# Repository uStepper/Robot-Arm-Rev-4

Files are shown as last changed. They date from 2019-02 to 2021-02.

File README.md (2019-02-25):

# Robot Arm Rev 4
STL files and instructions for uStepper Robot Arm Rev 4

The Robot Arm and uStepper actuators can be purchased on www.ustepper.com/shop

<br /><span xmlns:dct="http://purl.org/dc/terms/" property="dct:title">uStepper</span> by <a xmlns:cc="http://creativecommons.org/ns#" href="www.ustepper.com" property="cc:attributionName" rel="cc:attributionURL">ON Development</a> is licensed under a <a rel="license" href="http://creativecommons.org/licenses/by-nc-sa/4.0/">Creative Commons Attribution-NonCommercial-ShareAlike 4.0 International License</a>.

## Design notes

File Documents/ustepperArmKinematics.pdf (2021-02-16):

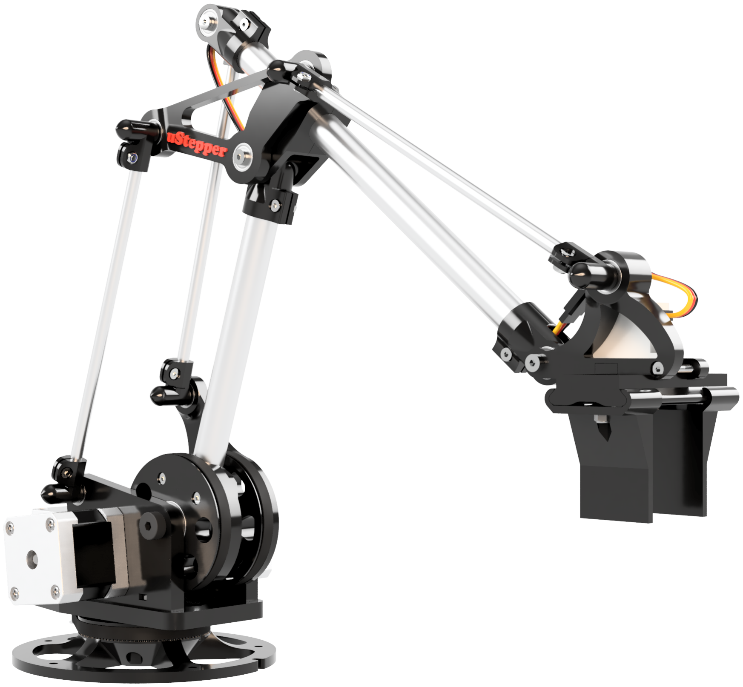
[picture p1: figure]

# uStepper Robot Kinematics

uStepper Robot Arm Rev 4 Kinematics

by Mogens Groth Nicolaisen

# Contents

1 uStepper Robot Arm Kinematics | 1

I

# uStepper Robot Arm Kinematics 1

To model the uStepper robot arm, first forward kinematic analysis is performed. The kinematic analysis is done analytical using basic trigonometry because of the Robot’s simple structure. D-H¹ with reference changing matrix transformations from world coordinates to end-effector could be done but is not required to derive kinematics for this simple setup.

## 1.1 Forward Kinematics

In the forward kinematics case, calculations are done to derive the end-effector point from a given set of actuator angles (θ). Figure 1.1 shows the basic geometry of the robot arm when looking from the side. Notice the offset from the end point to the "gripper" end point. This makes the model more generic when using different actuator types. An offset from this point to the actuator is required though. Another feature to notice is that when changing θ2
it is required to move both Primary and Secondary gear equally to maintain θ3
- this has to be accounted for in the implementation phase.

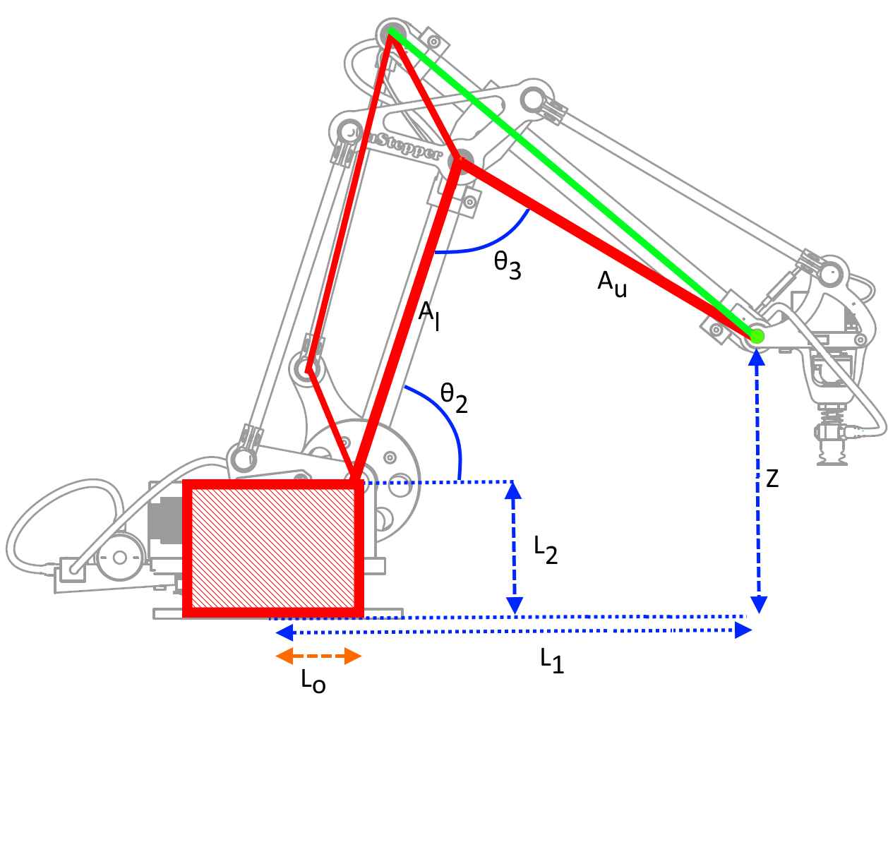
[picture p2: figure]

Figure 1.1: Side view of the robot, with simple graphics applied to help deriving the kinematic equations.

From Figure 1.5 it is easily seen that to account for the offset from end-point to actuator end-point an offset in Z and L1

is required. These are denoted Zo and L1o respectively and for the actuator on Figure 1.5 Zo would be negative while L1o would be positive. The offsets are omitted in the following derivations to ease the readability. In the code they are added.

1Denavit–Hartenberg
1

2 | Chapter 1. uStepper Robot Arm Kinematics

Using the geometry presented in Figure 1.1 Z is derived by adding right triangles resulting in the more detailed Figure 1.2

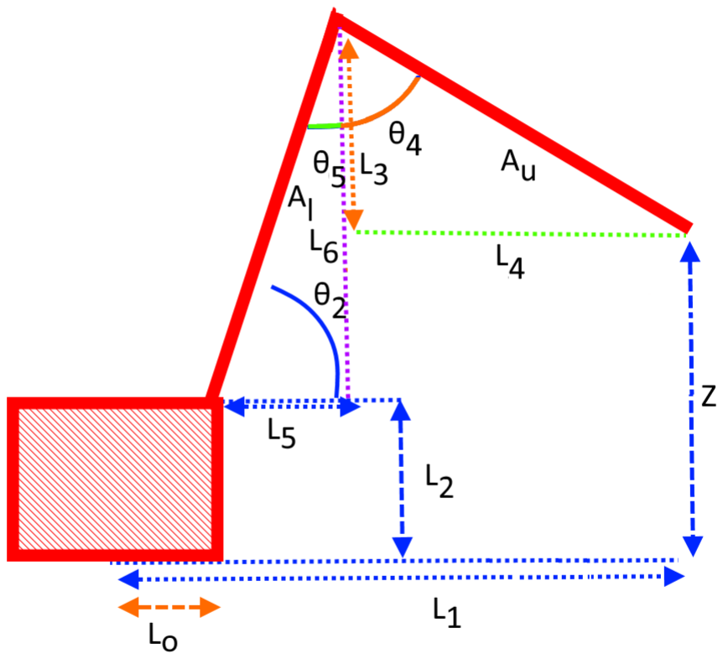
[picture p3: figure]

Figure 1.2: Side view of the robot arm representation for kinematics calculations.

Using Figure 1.2 Z will be derived as shown Equation (1.1):

Z = L2 + L6 − L3
[mm] (1.1)

Where L3 and L6 will be derived using simple trigonometry and L2 is a design parameter from Table 1.1. First L6

is derived in Equation (1.3)

sin(θ2

) = L6
Al

(1.2)

L6 = sin(θ2
)Al

[mm] (1.3)

To derive L3

it is required to know θ4

, which is possible to derive from θ5 found in Equation (1.4):

θ5 = 180◦ − (90◦ + θ2

) | [◦
] (1.4)

Where the 180◦

comes from the angle sum of a triangle, and the 90◦ | from the known right angle. The
angle θ2 was given as input to the forward kinematics as discussed previously. θ4
is derived in Equation (1.5):

θ4 = θ3 − θ5

| [ ◦
] (1.5)

And L3

is found from Equation (1.7)

cos(θ4

) = L3
Au

(1.6)

L3 = cos(θ4
)Au
| [mm] (1.7)

1.1. Forward Kinematics | 3

Z can now be derived using Equation (1.1) stated here again for convenience:

Z = L2 + L6 − L3 | [mm] (1.8)

Now that Z is derived, X and Y is left. To derive those the view is changed to the top view in Figure 1.3.

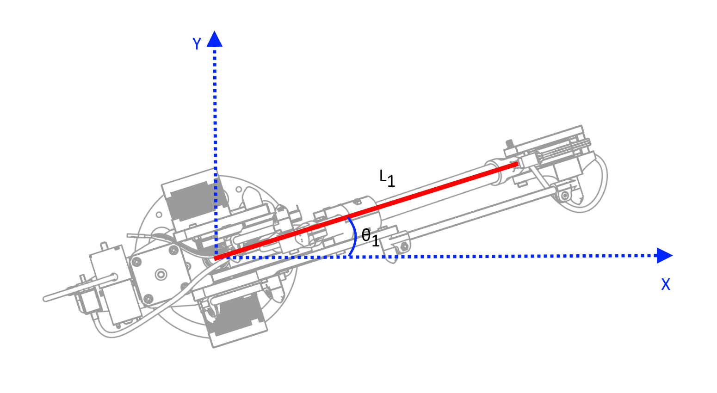
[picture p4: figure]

Figure 1.3: Top view of the robot arm with world coordinates on top.

As also shown on Figure 1.1, Figure 1.3 shows the stretch L1

. Additionally the rotation angle θ1 is marked
on Figure 1.3. Using simple trigonometry X and Y is derived in Equation (1.12).

cos(θ1

) = X
L1

(1.9)

X = cos(θ1
)L1

[mm] (1.10)

sin(θ1

) = Y
L1

(1.11)

Y = sin(θ1
)L1

[mm] (1.12)

Looking at Figure 1.2 it is obvious that L1 is the sum of L4 and L5

. L5

is derived using regular trigonometry in Equation (1.14).

cos(θ2

) = L5
Al

(1.13)

L5 = cos(θ2
)Al

[mm] (1.14)

And finally L4

is found from Equation (1.16).

sin(θ4

) = L4
Au

(1.15)

L4 = sin(θ4
)Au

[mm] (1.16)

Arriving at L1

in Equation (1.17).

L1 = L4 + L5 + Lo

[mm] (1.17)

4 | Chapter 1. uStepper Robot Arm Kinematics

Where Lo

is the constant offset from rotation center. To sum up, Z, X and Y is found by the following combined equations (from the previous derivations):

Z = L2 + L6 − L3 | [mm] (1.18)

Z = L2 + sin(θ2

)Al − cos(θ3 − (90◦ − θ2
))Au
| [mm] (1.19)

X = cos(θ1
)L1
| [mm] (1.20)

X = cos(θ1

)(sin(θ3 − (90◦ − θ2

## ))Au + cos(θ2 )Al + Lo

) | [mm] (1.21)

Y = sin(θ1
)L1
| [mm] (1.22)

Y = sin(θ1

)(sin(θ3 − (90◦ − θ2

## ))Au + cos(θ2 )Al + Lo

) | [mm] (1.23)

### 1.1.1 Summing Up

To implement the forward kinematics the former derived equations can be arranged to reduce computations required. This will be done in the following, and a code example will be presented.
The former enabled us to calculate the coordinates based on our angles θ1
| , θ2 and θ3 . But we intend to
read out motor angles, so we have to do a little conversions when reading motor angles:

θ1 = θM B

1
K

[

| ◦ ] (1.24)

θ2 = (θM E − θMS)

1
K

[

◦
] (1.25)

θ3 = θMS

1
K

[

◦
] (1.26)

where θM B is base motor angle, θM E is elbow motor angle, θMS is shoulder motor angle and K is the gear ratio which is the same for all three gears in this case. The inputs for the forward kinematics are then as derived from the motor angles:

- θ1
- rotation angle
- θ2
- shoulder angle
- θ3
- elbow angle

And the required equations are:

Z = L2 + sin(θ2

)Al − cos(θ3 − (90◦ − θ2
))Au

[mm] (1.27)

k1 = (sin(θ3 − (90◦ − θ2

## ))Au + cos(θ2 )Al + Lo

) | [ ] (1.28)

X = cos(θ1
)k1

[mm] (1.29)

Y = sin(θ1
)k1

[mm] (1.30)

A code example snippet is provided in the following (note that Zo and L1o are added here as discussed in Section 1.1):

1.2. Inverse Kinematics | 5
1 | // Pre−c a l c u l a t e d o f f s e t s i n motor an gle a t home p o s i t i o n
2 | #d e fi n e SHOULDEROFFSET 142.0 f
3 | #d e fi n e ELBOWOFFSET 45.0 f

4
5 | void u S te p pe rR o b o ti c s : : FWKinematic ( f l o a t& x , f l o a t& y , f l o a t& z , f l o a t thetaMB , f l o a t thetaME
| , f l o a t thetaMS ) //Forward ki nem a ti c s an gle To xyz
6 | {

7
8 | t he t a 1 = thetaMB∗1/K ;
9 | t he t a 2 = ( thetaME−thetaMS ) ∗1/K + ELBOWOFFSET ;
10 | t he t a 3 = thetaMS∗1/K + SHOULDEROFFSET ;

11
12 | t he t a 1 = t he t a 1 ∗ 3.1415 / 18 0.0 ; // To r a di a n s
13 | t he t a 2 = t he t a 2 ∗ 3.1415 / 18 0.0 ; // To r a di a n s
14 | t he t a 3 = t he t a 3 ∗ 3.1415 / 18 0.0 ; // To r a di a n s

15
16 | z = L2 + si n ( t he t a 2 ) ∗Al − co s ( t he t a 3 − (90 − t he t a 2 ) ) ∗Au + Zo ; // o f f s e t i n the Z di r e c t o n
| f o r the a c t u a t o r i s added here

17
18 | k1 = si n ( t he t a 3 − (90 − t he t a 2 ) ) ∗Au + co s ( t he t a 2 ) Al + Lo + L1o ; // o f f s e t i n the L1 di r e c t o n
| f o r the a c t u a t o r i s added here

19
20 x = co s ( t he t a 1 ) ∗k1 ;

21
22 y = si n ( t he t a 1 ) ∗k1 ;

23
24 }

Another thing to notice here is the offset added to ELBOW and SHOULDER - these offsets are defined by the home-position of the robot which is at the mechanical stops where the arm is retracted to towards the base

## 1.2 Inverse Kinematics

To control the robot end-effector reference positions are given in the world coordinate system, which then has to be translated to a given set of actuator angles achieving these reference positions. I.e. in the inverse kinematics case, the desired end-effector coordinates are known and from these the actuator angles must be derived.
The starting point of the inverse kinematics derivation is the rotation angle. Looking at Figure 1.4 it is obvious that simple trigonometry where a right angle triangle is constructed from the end of L1 down to the x-axis, can be used.

6 | Chapter 1. uStepper Robot Arm Kinematics

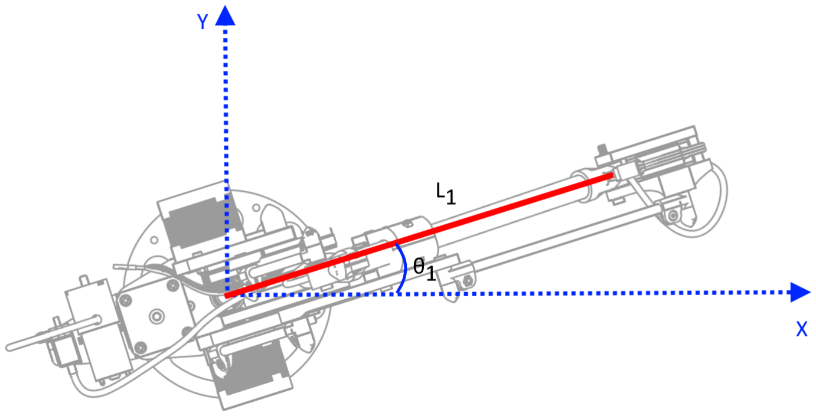
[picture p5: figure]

Figure 1.4: Top view of the robot arm with world coordinates on top.

To derive θ1 Equation (1.31) is used.

θ1 = a tan2 (Y, X) | [ ◦ ] (1.31)

Using a tan2 provides solutions for X = 0 and X < 0 as opposed to the regular arctangent function where solutions for these cases has to be handled separately.
For the next calculations the length of L1 | is required and therefore found in Equation (1.32).

L1 =

p
X² + Y ² | [mm] (1.32)

To derive the remaining two angles a new figure is constructed (Figure 1.5).

1.2. Inverse Kinematics | 7

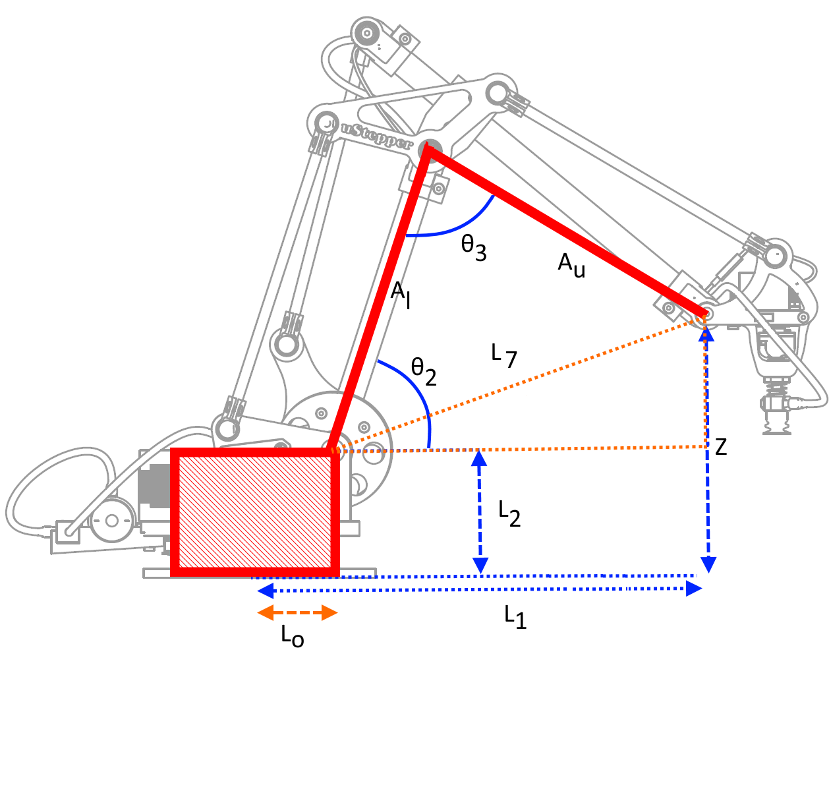
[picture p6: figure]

Figure 1.5: Side view of the robot, with simple graphics applied to help deriving the kinematic equations.

First θ3
is derived by use of the cosine rule which requires knowledge of L7 derived in Equation (1.33).

L7 =

Æ
(L1 − Lo
)

2 + (Z − L2
)
2 | [mm] (1.33)

For the next calculations a couple of solutions for trigonometric problems have to be considered:

cos(θ) = x → θ = a tan2

±

p
1 − x

2, x

| (1.34)

sin(θ) = x → θ = a tan2

x,±

p
1 − x

2

| (1.35)

As well as the cosine rule:

cos(A) = b

2 + c

2 − a

2
2bc
| (1.36)
| (1.37)

And θ3
can be found in Equation (1.39).

cos(θ3

) =
A

2
l

+ A

2
u − L

2
7
2AlAu
| (1.38)

θ3 = a tan2

±

vu
t
1 −
A

2
l

+ A²
u − L

2
7
2AlAu

2
,
A

2
l

+ A

2
u − L

2
7
2AlAu

- [

◦
] (1.39)

Chapter 1. uStepper Robot Arm Kinematics

θ2
can be found by a combination of the orange right angle triangle in Figure 1.5 and the triangle above that once again.

θ2 = a tan2

(Z − L2
)
L7
,±

vu
t
1 −
(Z − L2
)
L7

2

- (1.40)

+ a tan2

±

vu
t
1 −
L

2
7 + A

2
l

− A²
u
2L7Al

2
,
L

2
7 + A

2
l

− A

2
u
2L7Al

- [

◦
] (1.41)

### 1.2.1 Summing Up

Here it is required to calculate the motor angles from the actuator angles as well as the actuator angles were calculated from the motor angles in the forward kinematics case. So, θM B, θM E and θMS are derived from θ1

, θ2 and θ3 by the fllowing conversion:

θM B = θ1K | [

◦
] (1.42)

θM E = (θ2 + θ3
)K | [

◦
] (1.43)
θMS = θ3K | [

◦
] (1.44)

With implementation in mind a code example for the implementation is suggested. The inverse kinematics has X, Y and Z as input (note that Zo and L1o are added here as discussed in Section 1.1). To simplify matters the constants/offsets are subtracted as early as possible which is seen in the code snippet.

void u S te p pe rR o b o ti c s : : InvKinem a ti c ( f l o a t& the t a1 , f l o a t& the t a2 , f l o a t& the t a3 , f l o a t x , f l o a t y , f l o a t z ) // xyz To Angle s

{
x = x − co s ( t he t a 1 ) ∗L1o ;
y = y − si n ( t he t a 1 ) ∗L1o ;
z = z − Zo − L2 ;

t he t a 1 = a tan2 ( y , x ) ; // r o t a t i o n i s denoted as t he t a 1 i n the documen ta tion .

f l o a t L1 = s q r t ( x∗x + y∗y ) − Lo ;

f l o a t L7 = s q r t ( L1∗L1 + z∗z ) ;

f l o a t a = z/L7 ;
f l o a t b = ( L7∗L7 + Al ∗Al − Au∗Au) /(2∗L7∗Al ) ;
f l o a t c = ( Al ∗Al + Au∗Au − L7∗L7 ) /(2∗ Al ∗Au) ;

t he t a 2 = ( a tan2 ( a , s q r t (1 − a∗a ) ) + a tan2 ( s q r t (1 − b∗b ) , b ) ) ;

t he t a 3 = a tan2 ( s q r t (1 − c∗c ) , c ) ;

t he t a 1 = t he t a 1 ∗ 180 / 3.1415 ; // To Degree
t he t a 2 = ( t he t a 2 − ELBOWOFFSET) ∗ 180 / 3.1415 ; // To Degree t he t a 3 = ( t he t a 3 − ELBOWOFFSET) ∗ 180 / 3.1415 ; // To Degree

1.3. Implementation | 9
25 | thetaMB = t he t a 1 ∗ K ;
26 | thetaME = ( t he t a 2+t he t a 3 ) ∗ K ;
27 | thetaMS = t he t a 3 ∗ K ;

28
29 }

Here we also took the initial angles of elbow and should into account as we did in the forward kinematics.

## 1.3 Implementation

In this section the implementation will be discussed. This includes looking at the physical system - the uStepper Robot Arm Rev 4, and deriving the constants neede for the forward and inverse kinematics.

### 1.3.1 Predefined Constants

A table of constants is generated for use in the calculations (Table 1.1).

Variable | Value | Description
Al Au L2 Lo L1o Zo SHOU LDEROF FSET E LBOW OF FSET | 182 mm 188 mm 73 mm 47 mm 40 mm −70 mm 142◦ 45◦ | Lower arm length Upper arm length Height from base to gears horizontal axis Offset in the L1 direction Actuator offset in L1 direction Actuator offset in Z direction Shoulder angle offset in home position Elbow angle offset in home position

Table 1.1: Constants required for kinematic calculations.

The constants are found on the robot arm as shown in Figure 1.6.

10 | Chapter 1. uStepper Robot Arm Kinematics

Figure 1.6: Side view of the robot, with simple graphics applied to show the constants use in the calculations.

The constants in Table 1.1 is derived by measuring the robot as shown on Figure 1.6. Furthermore the measurements Lt1

, Lt2

, Lt3 and Lt4 are shown here to emphasize that the pairwise have to be of equal length, e.g. the ones marked Lt1

is required to be of equal length as well as the two Lt2 etc. This is required to get the benefits of having two parallelograms as part of the robots mechanical structure.

### 1.3.2 Gear Ratios

All calculated angles from the kinematics are subject to a gear ratio calculation to e.g. get the inverse kinematic angles to motor angles. The gear ratio is the same for all three axis on the uStepper Robot Arm Rev 4 - 5.1 : 1. As an example, the calculated θ1
from the inverse kinematics would be multiplied by 5.1 before it is sent on to the motor. In the former example code snippets the gear ratio was denoted K.

### 1.3.3 Physical Limitations

It is quite important to implement functionality that includes the robots physical limitations in the calculations. E.g. a world coordinate of (1, 1, 0)mm is not possible to reach since that is some place in the robot frame. It is obvious from the previous discussions and Figure 1.2 (shown again in Figure 1.7) that it is not possible for the arm to reach within Lo of 47 mm from the base - and more has to be added because of other physical limitations.

1.3. Implementation | 11

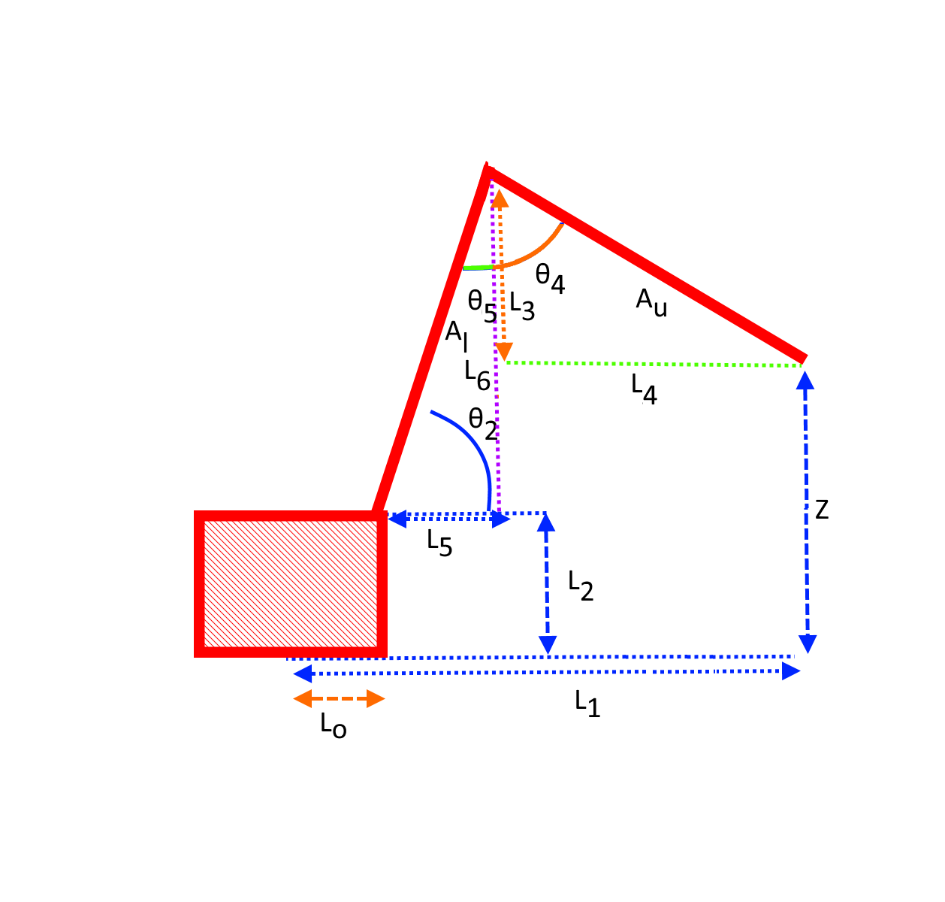
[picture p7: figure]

Figure 1.7: Side view of the robot arm representation for kinematics calculations.

Limitations will be handled in joint space and thus the following limitations to angles must be considered:

- Limit1: The gear angles can never go negative.
- Limit2: The secondary gear must be kept behind the main gear by 2◦ to avoid collision between the gears.
- Limit3: From homing the rotating axis θ1 it is necessary to limit it to going between 0◦

and 358◦
because of the mechanical stop.
- Limit4: The main gear (shoulder) must never go below 10◦ from horizontal (i.e. θ2 must always be larger than 10◦
) to avoid skewing the parallelograms of the robot.
1 | // Func tion f o r chec kin g the c o n s t r a i n t s on the r o b o t be f o re moving − we can
2 | // decide t o e i t h e r move t o c l o s e s t p o s s i b l e or r e t u r n f a u l t
3 | bool u S te p pe rR o b o ti c s : : c h e c k Limi t s ( f l o a t r o t , f l o a t l e f t , f l o a t r i g h t ) {
4 | // l i m i t #1: gea r a n gle s must always be p o s i t i v e
5 | i f ( ( r o t || l e f t ) < 0 && r i g h t > 0) {
6 | r e t u r n 0 ;
7 | }
8 | // l i m i t #2: keep elbow gea r behind sh oulde r gea r a t a l l time s t o avoid
9 | // c o l l i s i o n between gea r and main arm . 2 deg motor an gle i n a d di ti o n t o
10 | // homing an gle should s u f f i c e
11 | e l s e i f ( ( l e f t − 2) >= r i g h t ) {
12 | r e t u r n 0 ;
13 | }

12 | Chapter 1. uStepper Robot Arm Kinematics
14 | // l i m i t #3: r o t a t i o n can only go from 0 t o 358 degree because o f hard s t o p
15 | e l s e i f ( r o t > 358 ∗ GEARRATIO) {
16 | r e t u r n 0 ;
17 | }
18 | // l i m i t #4: main gea r ( sh oulde r ) must neve r go below 10 de g ree s from
19 | // h o r i z o n t al t o avoid skewing the p a r all el o g r am s o f the r o b o t
20 | e l s e i f ( r i g h t > 80) {
21 | r e t u r n 0 ;
22 | } e l s e {
23 | r e t u r n 1 ;
24 | }
25 | }

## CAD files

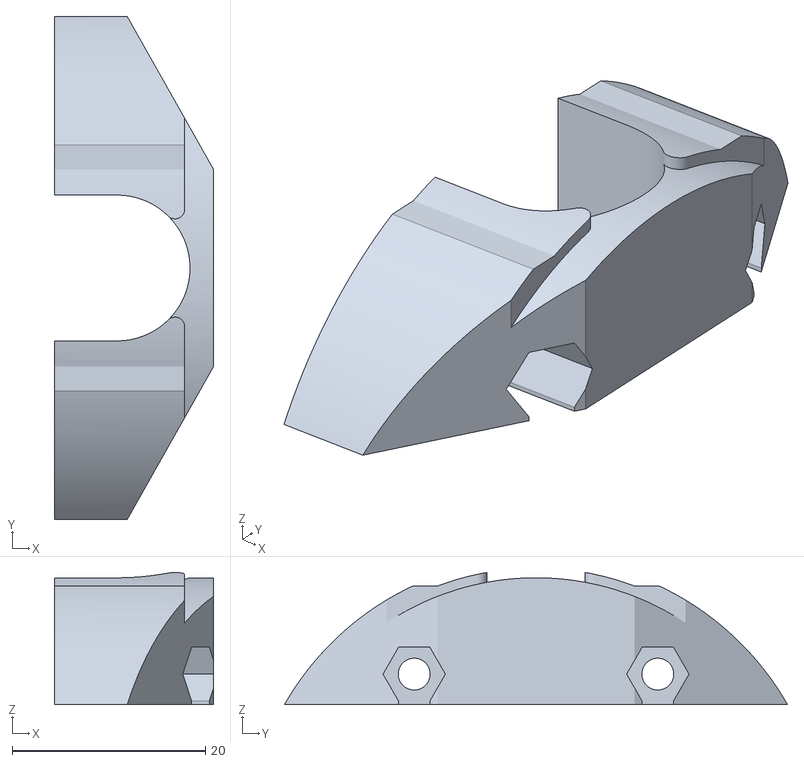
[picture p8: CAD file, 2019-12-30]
STL Package/7-Main Gear Bracket.stl
16.5 x 52.1 x 13.7

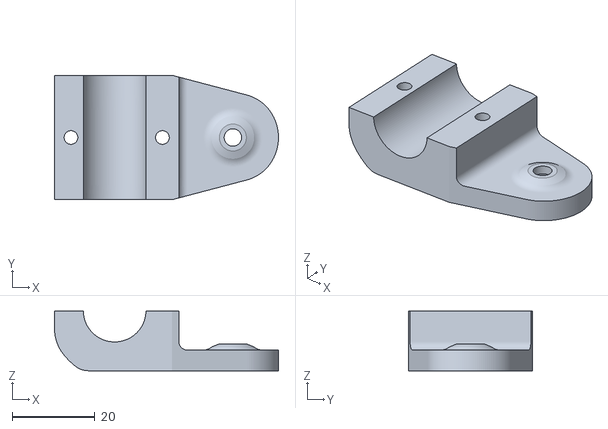
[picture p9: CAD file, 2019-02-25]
STL Package/8-Main Bracket Nutside.stl
54.0 x 30.0 x 14.4

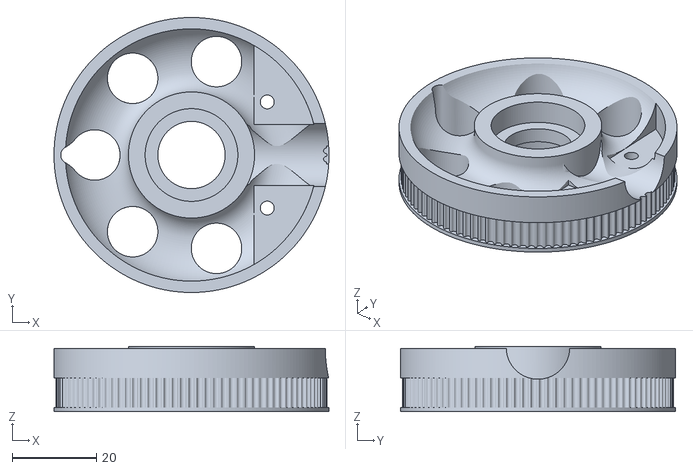
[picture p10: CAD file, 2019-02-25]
STL Package/6-Main Gear.stl
65.4 x 65.4 x 15.5

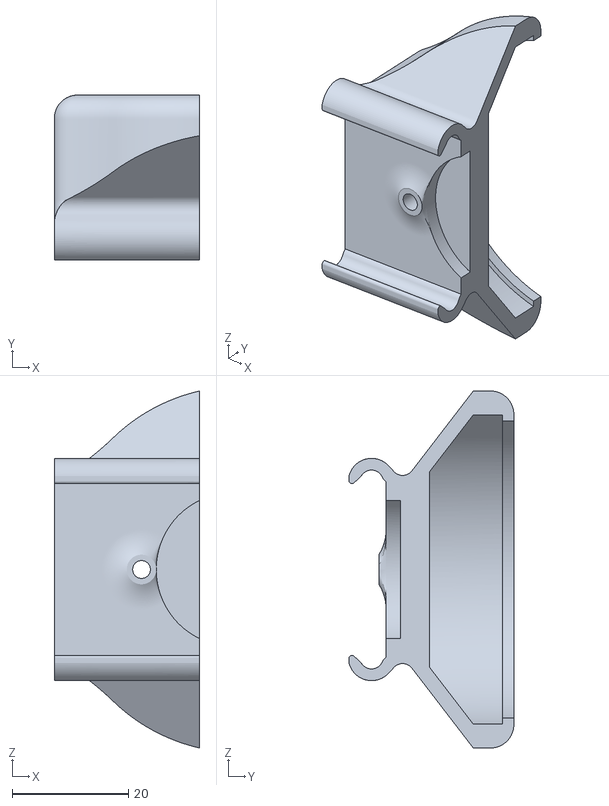
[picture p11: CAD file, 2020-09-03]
End Effectors/Can Gripper/Gripper.stl
25.0 x 28.4 x 61.4

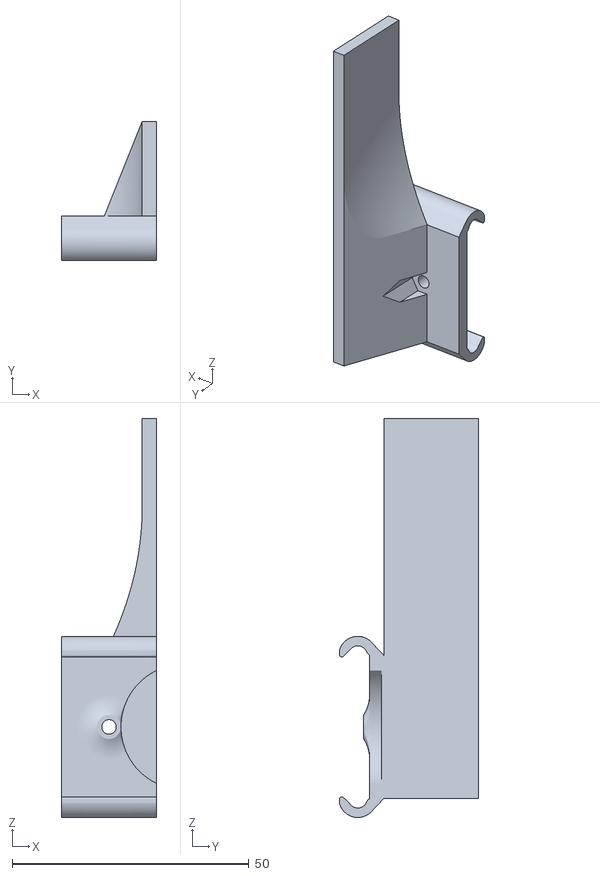
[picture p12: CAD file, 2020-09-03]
End Effectors/Horizontal/Gripper.stl
20.0 x 29.4 x 84.2

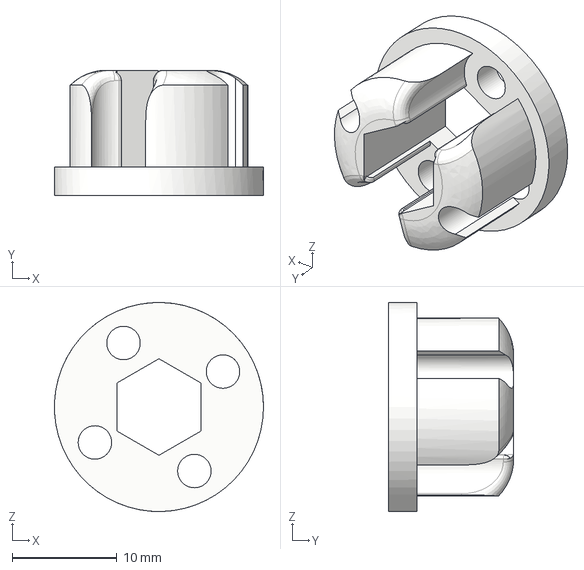
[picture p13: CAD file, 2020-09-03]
End Effectors/Vacuum/Rotation Bracket.step
20.0 x 12.0 x 20.0 mm

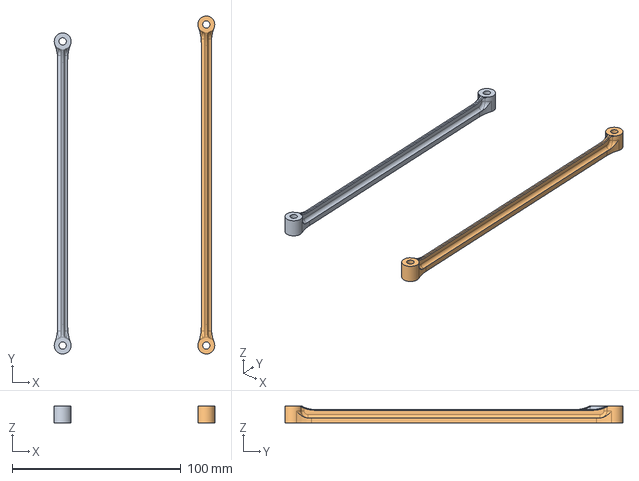
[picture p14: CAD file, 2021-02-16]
STEP/Printed_6mm_links.step
95.0 x 200.0 x 10.0 mm

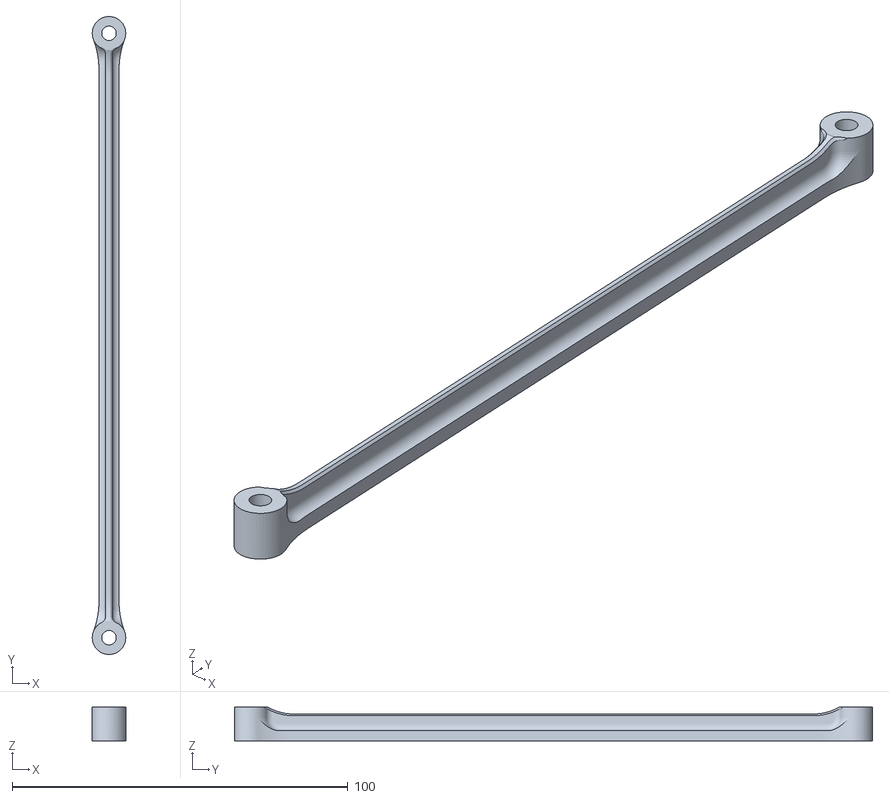
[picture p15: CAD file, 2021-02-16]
STL Package/180mm.stl
10.00 x 190.0 x 10.0

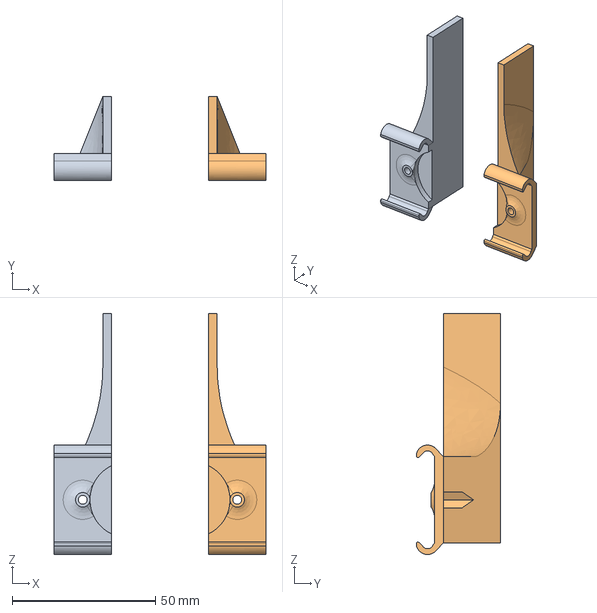
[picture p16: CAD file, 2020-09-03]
End Effectors/Horizontal/Horizontal gripper.step
74.0 x 29.4 x 84.2 mm
Gripper
Gripper(Mirror)

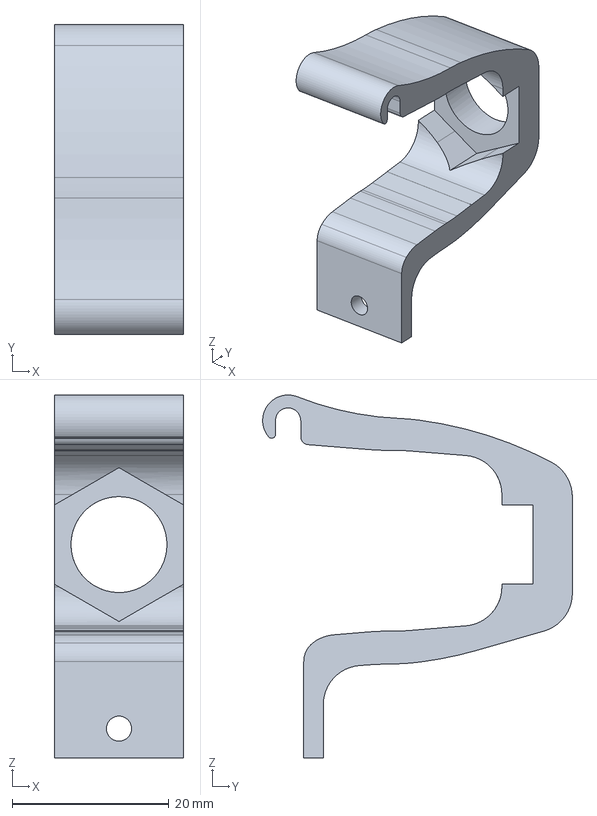
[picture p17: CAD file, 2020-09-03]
End Effectors/Vacuum/Suction Bracket.step
16.5 x 39.5 x 46.3 mm

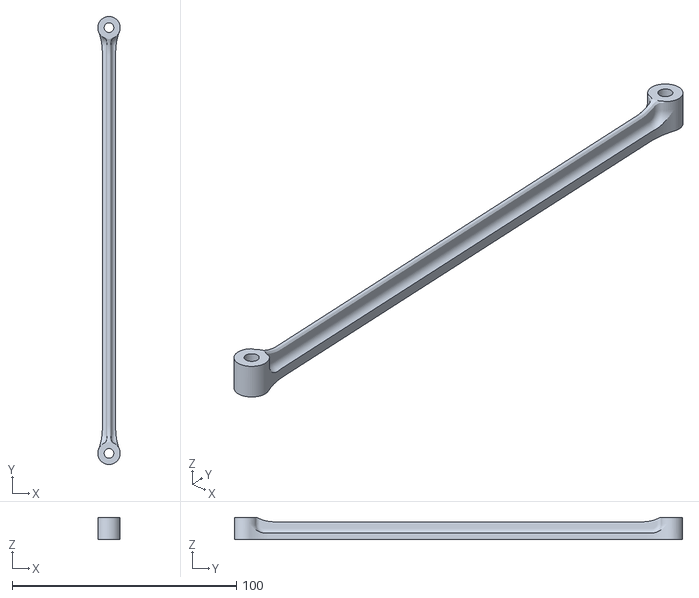
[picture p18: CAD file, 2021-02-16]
STL Package/190mm.stl
10.00 x 200.0 x 10.0

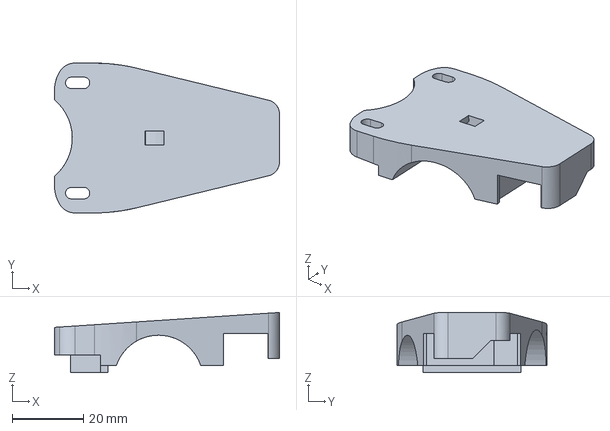
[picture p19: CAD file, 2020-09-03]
End Effectors/Vacuum/Vacuum Pump Bracket.step
63.2 x 42.1 x 16.9 mm

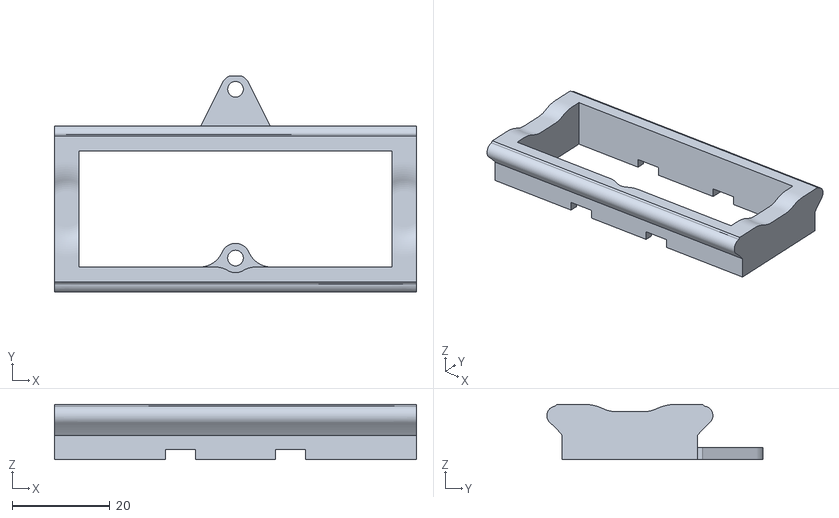
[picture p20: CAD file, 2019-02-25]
STL Package/18-Gripper Slide.stl
74.0 x 44.2 x 11.3

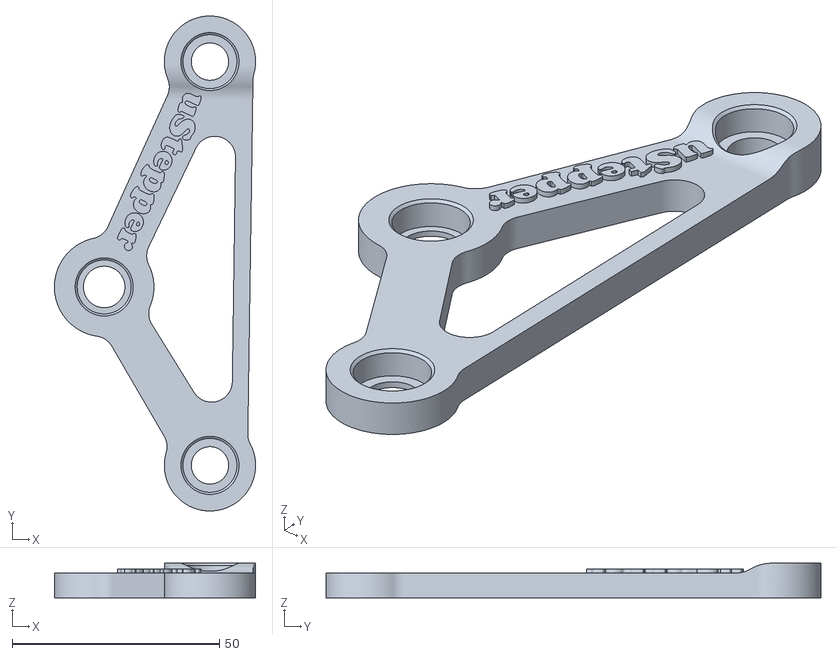
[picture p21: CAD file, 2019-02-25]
STL Package/12-Triangle.stl
48.5 x 119.3 x 8.35

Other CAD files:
End Effectors/Can Gripper/Can gripper.step
STL Package/15-End Effector Right.stl
STL Package/10-Rod End 15mm.stl
STL Package/5-Secondary Gear.stl
End Effectors/Vacuum/Rotation Bracket.stl
End Effectors/Vacuum/Suction Bracket.stl
End Effectors/Vacuum/Vacuum Pump Bracket.stl
STL Package/11-Rod End 6mm.stl
STL Package/16-End Effector Left.stl
STL Package/17-End Effector Bottom.stl
STL Package/19-Gripper.stl
STL Package/2-Structure Bottom.stl
STL Package/20-Gripper Arm.stl
STL Package/3-Structure Left Side.stl
STL Package/4-Structure Right Side.stl
STL Package/9-Main Bracket Boltside.stl

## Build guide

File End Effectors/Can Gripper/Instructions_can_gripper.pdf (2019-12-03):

# Can Gripper

# uStepper Robot Arm 4.0

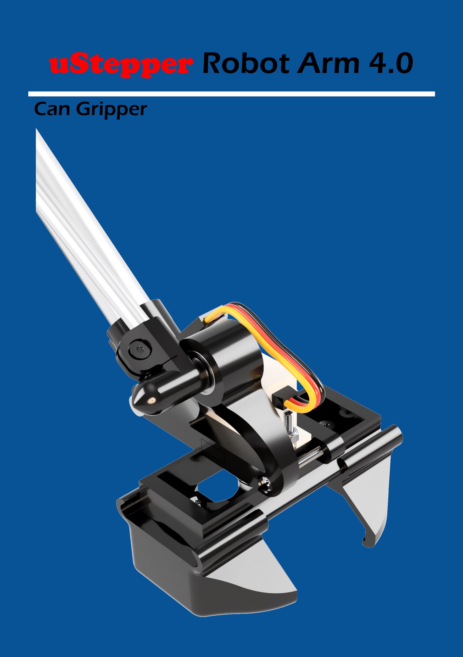
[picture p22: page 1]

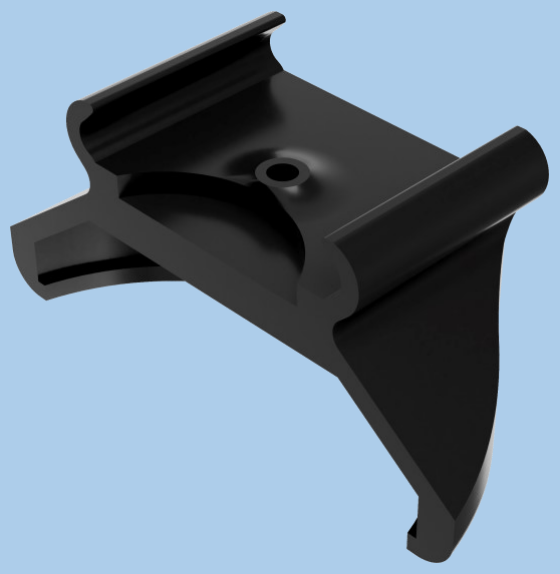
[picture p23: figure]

## 2 x Can Gripper

# Bill Of Materials

# Dimensions (mm)

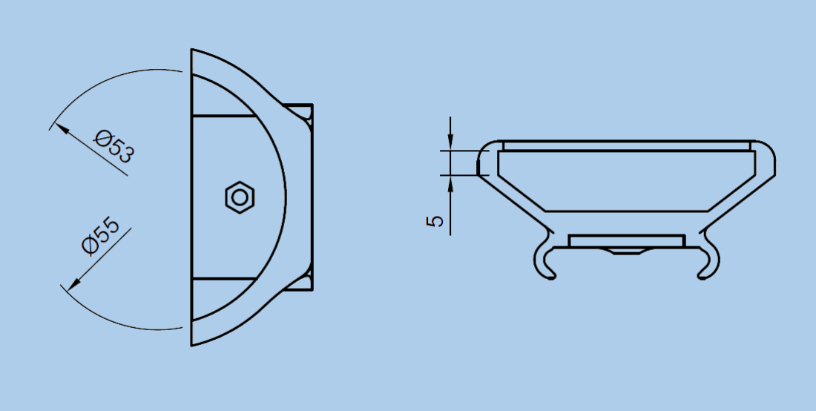
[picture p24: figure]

# Disassembly of standard gripper

1

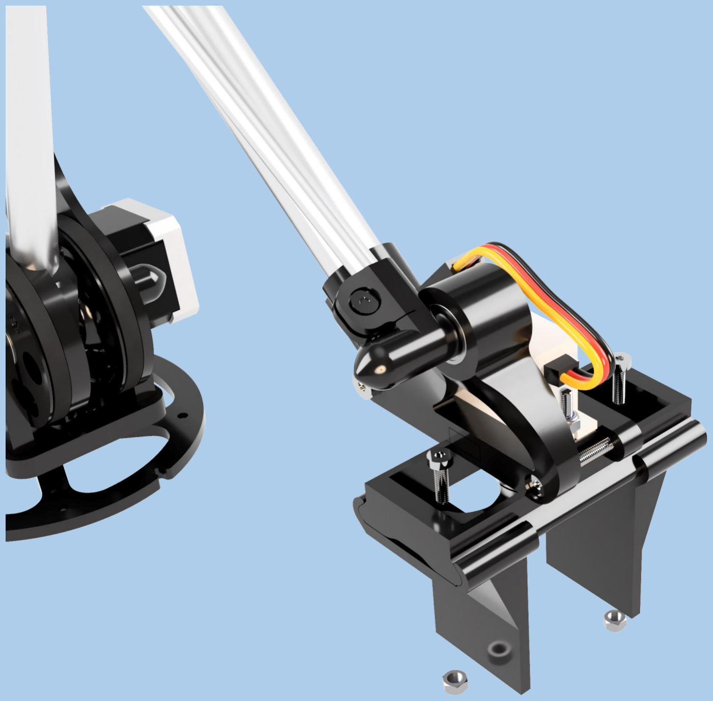
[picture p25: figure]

2

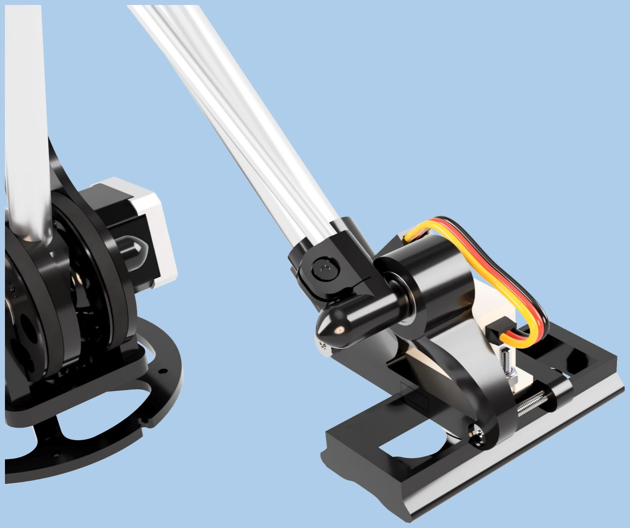
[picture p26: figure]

# Assembly of Can Gripper

2x

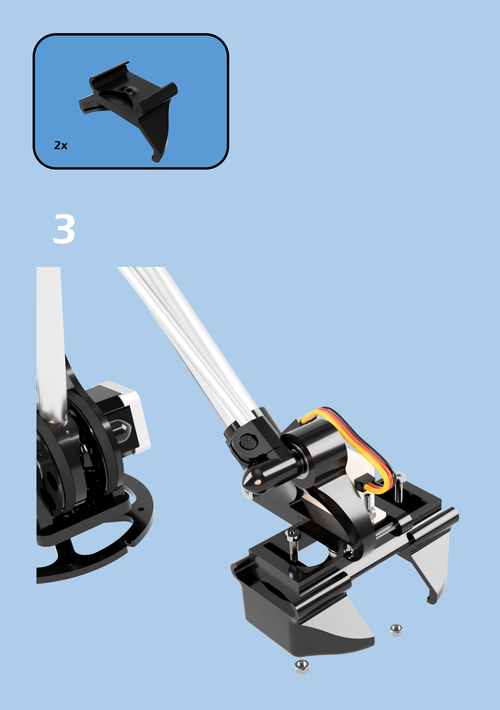
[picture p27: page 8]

3

4

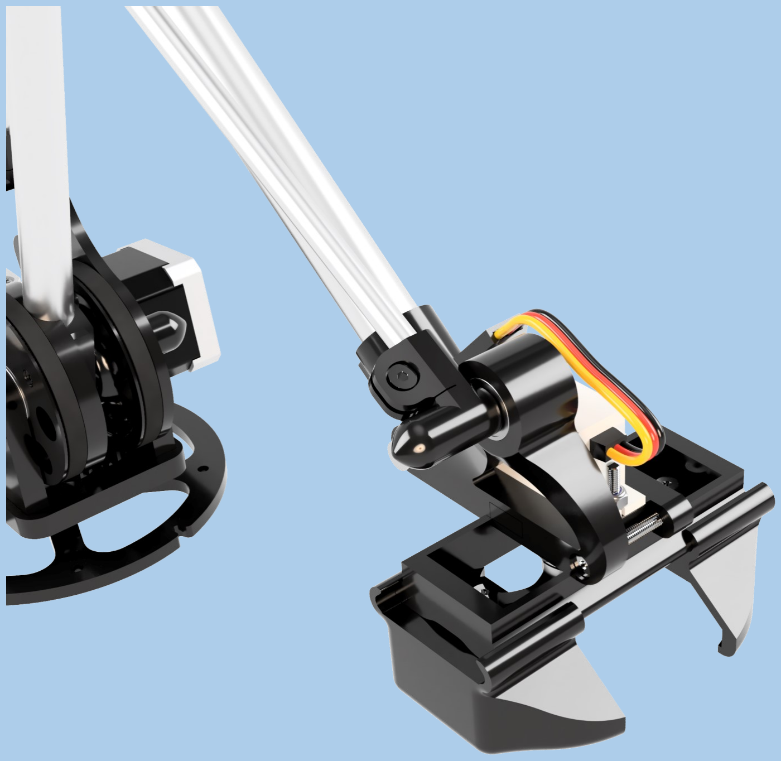
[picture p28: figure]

# Disclaimer

1 Disclaimers and Limitation of Liability

1.1 uStepper ApS and/or ON Development IVS (or any individuals affiliated with either of the two companies) can not be held responsible for any damage inflicted upon mounting or interfacing with uStepper products This also includes damage to stepper motors (both electrical and mechanical) or any other 3rd party hardware connected to or interfacing with any uStepper products. Most stepper motor cases are made of aluminum, and care must be taken when preparing the mountings for uStepper.

1.2 uStepper ApS and/or ON Development IVS (or any individuals affiliated with either of the two companies) can not be held responsible for any damage inflicted upon assembly of the uStepper Robot Arm. This includes damage to 3D printed parts, which must be considered to be of prototyping quality compared to injection moulded parts. Care must be taken while assembling 3D printed parts, and use of excessive force may lead to damage of the parts.

1.3 By using the uStepper products (including, but not limited to, hardware and software) you acknowledge that uStepper ApS and/or ON Development IVS (or any individuals affiliated with either of the two companies) can not be held responsible for any personal injuries and/or damage to any 3rd party hardware that may occur when using the uStepper products.

1.4 To the extent permitted by law, uStepper ApS and/or ON Development IVS will not be liable for any indirect or consequential loss or damage, of any kind, (including without limitation loss of business, opportunity, data, profits) arising out of or in connection with the use of any products (including, but not limited to, hardware and software), developed, produced or sold by uStepper ApS and/or ON Development IVS (or any individuals affiliated with either of the two companies).

1.5 Nothing in these Terms and Conditions shall be construed so as to hold uStepper ApS and/or ON Development IVS liable for death or personal injury as a result of the negligence of uStepper ApS and/or ON Development IVS or that of its employees or agents.

2 Indemnity

2.1 You agree to indemnify and hold uStepper ApS and/or ON Development IVS and its employees and agents harmless from and against all liabilities, legal fees, damages, losses, costs and other expenses in relation to any claims or actions brought against uStepper ApS and/or ON Development IVS arising out of any breach by you of these Terms and Conditions or other liabilities arising out of your use of this Website.

2.2 You agree to indemnify and hold uStepper ApS and/or ON Development IVS and its employees and agents harmless from and against all liabilities, legal fees, damages, losses, costs and other expenses in relation to any claims or actions brought against uStepper ApS and/or ON Development IVS arising out of any breach by you of these Terms and Conditions or other liabilities arising out of your use of products(including, but not limited to, hardware and software) developed, produced or sold by uStepper ApS and/or ON Development IVS (or any individuals affiliated with either of the two companies).

3 Severance

If any of these Terms and Conditions should be determined to be invalid, illegal or unenforceable for any reason by any court of competent jurisdiction then such Term or Condition shall be severed and the remaining Terms and Conditions shall survive and remain in full force and effect and continue to be binding and enforceable.

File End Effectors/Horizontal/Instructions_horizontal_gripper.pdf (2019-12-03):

# Horizontal Gripper

# uStepper Robot Arm 4.0

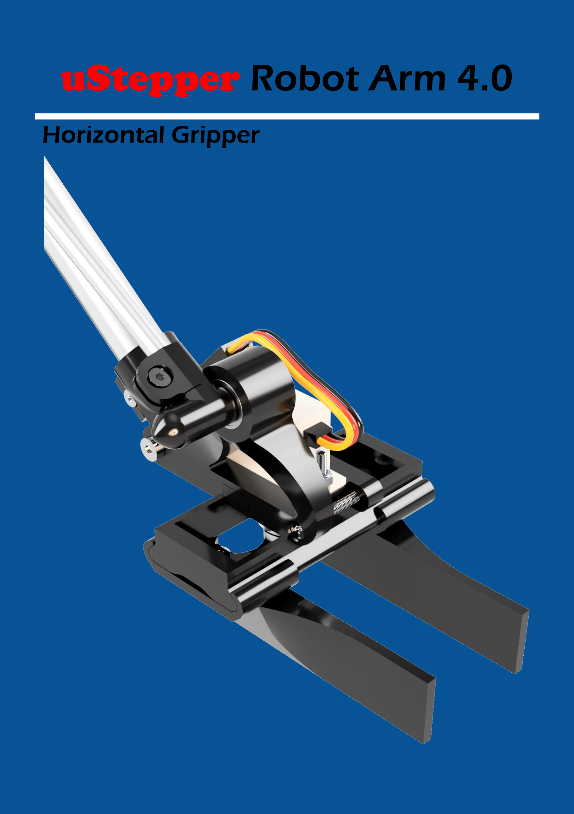
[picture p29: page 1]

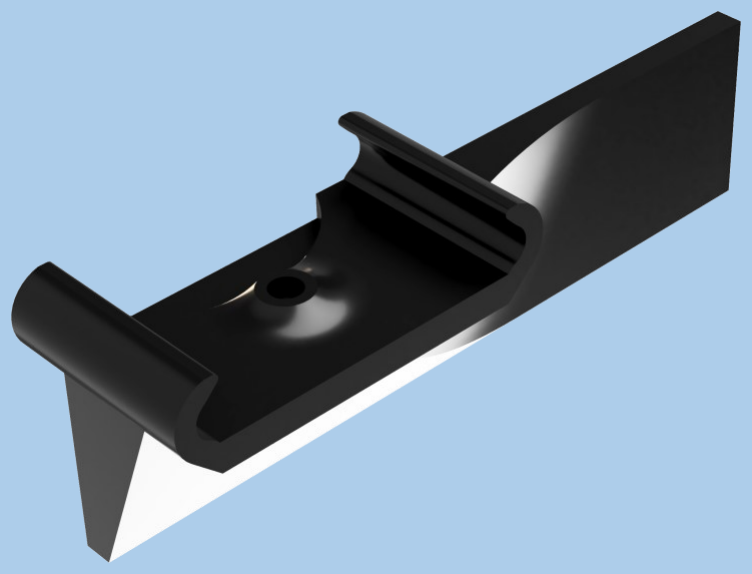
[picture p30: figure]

## 1 x Horizontal Gripper Right

# Bill Of Materials

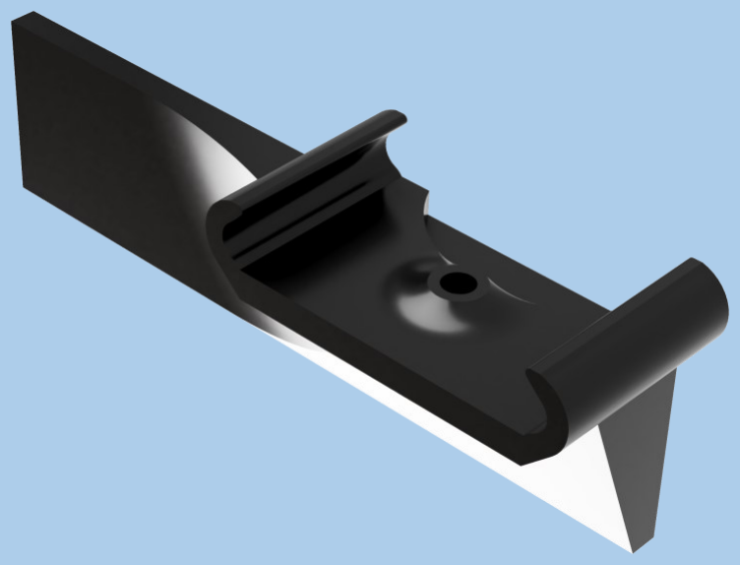
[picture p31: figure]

## 1 x Horizontal Gripper Left

# Dimensions (mm)

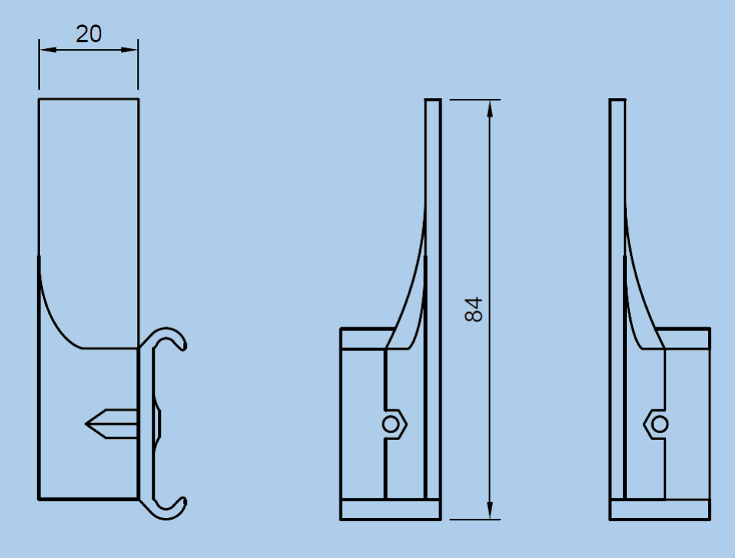
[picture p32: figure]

# Disassembly of standard gripper

1


2


# Assembly of Horizontal Gripper

1x | 1x

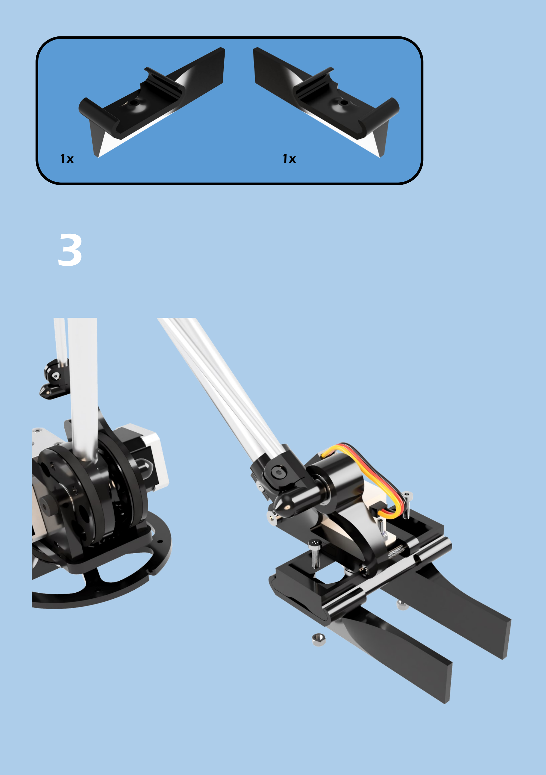
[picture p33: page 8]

3

4

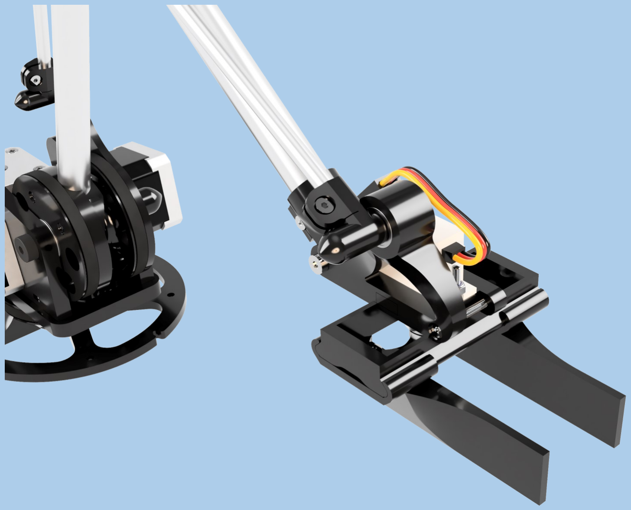
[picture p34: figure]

# Disclaimer

1 Disclaimers and Limitation of Liability

1.1 uStepper ApS and/or ON Development IVS (or any individuals affiliated with either of the two companies) can not be held responsible for any damage inflicted upon mounting or interfacing with uStepper products This also includes damage to stepper motors (both electrical and mechanical) or any other 3rd party hardware connected to or interfacing with any uStepper products. Most stepper motor cases are made of aluminum, and care must be taken when preparing the mountings for uStepper.

1.2 uStepper ApS and/or ON Development IVS (or any individuals affiliated with either of the two companies) can not be held responsible for any damage inflicted upon assembly of the uStepper Robot Arm. This includes damage to 3D printed parts, which must be considered to be of prototyping quality compared to injection moulded parts. Care must be taken while assembling 3D printed parts, and use of excessive force may lead to damage of the parts.

1.3 By using the uStepper products (including, but not limited to, hardware and software) you acknowledge that uStepper ApS and/or ON Development IVS (or any individuals affiliated with either of the two companies) can not be held responsible for any personal injuries and/or damage to any 3rd party hardware that may occur when using the uStepper products.

1.4 To the extent permitted by law, uStepper ApS and/or ON Development IVS will not be liable for any indirect or consequential loss or damage, of any kind, (including without limitation loss of business, opportunity, data, profits) arising out of or in connection with the use of any products (including, but not limited to, hardware and software), developed, produced or sold by uStepper ApS and/or ON Development IVS (or any individuals affiliated with either of the two companies).

1.5 Nothing in these Terms and Conditions shall be construed so as to hold uStepper ApS and/or ON Development IVS liable for death or personal injury as a result of the negligence of uStepper ApS and/or ON Development IVS or that of its employees or agents.

2 Indemnity

2.1 You agree to indemnify and hold uStepper ApS and/or ON Development IVS and its employees and agents harmless from and against all liabilities, legal fees, damages, losses, costs and other expenses in relation to any claims or actions brought against uStepper ApS and/or ON Development IVS arising out of any breach by you of these Terms and Conditions or other liabilities arising out of your use of this Website.

2.2 You agree to indemnify and hold uStepper ApS and/or ON Development IVS and its employees and agents harmless from and against all liabilities, legal fees, damages, losses, costs and other expenses in relation to any claims or actions brought against uStepper ApS and/or ON Development IVS arising out of any breach by you of these Terms and Conditions or other liabilities arising out of your use of products(including, but not limited to, hardware and software) developed, produced or sold by uStepper ApS and/or ON Development IVS (or any individuals affiliated with either of the two companies).

3 Severance

If any of these Terms and Conditions should be determined to be invalid, illegal or unenforceable for any reason by any court of competent jurisdiction then such Term or Condition shall be severed and the remaining Terms and Conditions shall survive and remain in full force and effect and continue to be binding and enforceable.

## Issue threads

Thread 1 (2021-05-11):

Kinematics Document Missing Lt1, Lt2, Lt3, Lt4

DanielJamesEvans, 2021-05-11:
Below Figure 1.6 of the kinematics document is this text: "_the measurements Lt1, Lt2, Lt3 and Lt4 are shown here_".  However, the figure doesn't show these measurements.  The Instructables webpage has a version of the figure that shows the labels.  I assume this figure was intended to also be included in the kinematics document?

I'm very impressed by this project; the documentation is stellar, and the robot itself seems very well-designed.  Thanks a lot for making the files available- it's a huge benefit to the community!

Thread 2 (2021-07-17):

what is difference between rev3 and rev 4 . By the way , thankyou for such an awesome stuff! :)

shubhmak, 2021-07-17:
i was just windering what is the difference between rev3 and rev 4 of the arm..... just curious (and a bit lazy too lol).

uStepper, 2021-07-17:
Hi,
The gears have been switched to belt drives from 3 to 4, more stability has been added by using thrust bearings and a lot of work went into optimizing the design to minimize unique parts in the design. Almost all the plastic parts were redesigned but based on the old look.

Best regards,
Mogens

Closed 2021-07-17.

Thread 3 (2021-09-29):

Rod end for 8 and 16 mm tube

IvolgaDmitriy, 2021-09-29:
Dear creators,
Unfortunately, I was not finding 6 and 15 mm tube in my area. I made new version rod end #10 and #11 for uStepper v4. I think it will be useful. New rod end for 16 mm and 8 mm tube.
Thank you for nice robot.

[10_11-Rod_End.zip](https://github.com/uStepper/Robot-Arm-Rev-4/files/7254698/10_11-Rod_End.zip)

IvolgaDmitriy, 2021-09-29:
> Dear creators, Unfortunately, I was not finding 6 and 15 mm tube in my area. I made new version rod end #10 and #11 for uStepper v4. I think it will be useful. Thank you for nice robot. Uploading 10_11-Rod_End.zip…

IvolgaDmitriy, 2021-09-29:
[10_11-Rod_End.zip](https://github.com/uStepper/Robot-Arm-Rev-4/files/7254694/10_11-Rod_End.zip)
16 and 8 mm

Closed 2024-06-19.

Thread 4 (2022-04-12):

Inverse Kinematics Issue

ThePaddingtonBear, 2022-04-12:
The radius of the joint that controls the angle of the lower arm (where the gripper is attached) on the moroe side is 65mm in STEP model. The radius of the linkage is roughly 75mm. Therefore the angle theta3 that is calculated in the kinematics can't be identical to the motor angle, right? There is like a non linear mechanical ratio between these 2 points, because they don't form an exact parallelogram.

I looked at similar robots like the industrial Kuka KR 40, where all joint distances are equal in length.

I might be missing something, but I think there might be a error.

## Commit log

2019-02-25 Assembly instructions with BOM added
2019-02-25 Added STL files
    [10-Rod End 15mm.stl, 11-Rod End 6mm.stl, 12-Triangle.stl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]
2019-05-16 Step file added
    Step file for the complete robot w. gripper added.
2019-12-30 updated maingear bracket
    tighter M3 nut reces
    [7-Main Gear Bracket.stl]
2020-09-03 3D files added
    [Can gripper.step, Gripper.stl]
2020-09-03 Updated two 3D files
    [Rotation Bracket.step, Rotation Bracket.stl]
2021-02-16 Added printed links
    Replacement for aluminium links - more robust and less parts needed.
    [180mm.stl, 190mm.stl, Printed_6mm_links.step]
2021-02-16 Updated kinematics document
    Added more details and more info in the code snippets
2021-02-21 updated length of tube required
